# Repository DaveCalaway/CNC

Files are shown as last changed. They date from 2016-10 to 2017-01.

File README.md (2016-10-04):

##Improvement for Chinese 50W CO2 Laser Engraving Cutting Machine

This project was born for replace the original electronic chinese card, that moved the laser cutter machine, with **RAMPS 1.4** or **Arduino CNC Shield** .  
In addiction i made DIY driver for a much more laser power, take a look at "DIY_Driver_Controller" folder.  

Now the laser cutter machine can work with G-Code and Laser-Web app.

**The same principle is apply for all CNC/laser machines.**

**Status**: *beta*  

##Schematics
We have three types of schematics:
- Chinese original schematic
- RAMPS schematic
- CNC Shield schematic

##Meaning of the  laser's signals
The original schematic of RAMP at *original_diagram* reported two differents signals for the laser:
- **Laser Fire**, in my case, is the *Enable* switch for a laser, it's boolean.  
  In the *Chinese original schematic* is the green line, from electronic card "LO" to Laser Power Supply "TL". Active low for laser on.  
  You can also send this signal to the *Front Pannel*.  
  In the *RAMPS_schematic* it's "D5" pin.  
  In the *CNC Shield* it's GND if you used LO or 5V is you used TL.  

- **Laser PWM**, in my cose, is the PWM signal to drive the power's ramp.  
  In the *Chinese original schematic* is the white line, from *Frontal Pannel* to *Laser Power Supply* "IN".  

  In the *RAMPS_schematic* it's "D4" pin.  

  In the *CNC Shield*:
  * V3.0 it's "Z+"" pin end stop.
  * V3.1 it's "SpnDir" pin.  

##RAMPS 1.4 & CNC Shield built in

Remeber, CNC Shield works with GRBL and RAMPS works with Marlin. The only real different are the command: http://goo.gl/lHQ7T  

###Diode advise [ RAMPS ONLY ]
Ensure that the Power Supply 5v rail is connected to RAMPS I2C 5v pin and that the D1 diode is removed from the RAMPS board as shown in the wiring diagram. If this pin is not connected the laser will fire when you disconnect your ramps board from USB power.  

###Motors & Movement config
In my Laser cutter machine, *Chinese card*, i have 2 motors:  
1. **X-Motor**, Flexible flat ( Ribbon ) white cable with two Opto Endstops(X and Y).  
2. **Y-Motor**, 4 wires cable.  

In addiction i have one other motor, **Z-Motor**, for rise up and down the base.  

The motors are: **17hw4410n-03ad-z** and **17hw3448n-15ad**  
I written to *baolongmotor* and they gave me the datasheet. Take a look in my repository.  

###Voltage Ref
Reference [Page](http://goo.gl/8VKoRP)  
For *resistors*: R100 = 0.1 Ohm or R200 = 0.2 Ohm ecc....  
In my case, the *formula* goes:  `IRef = Vref/( 8 * 0.1)`  

For my motors i need about *Y-Vref* = 0,8 * 0,48A = 0,4V  and  *X-Vref* = 0,8 * 1A = 0,8V  

###Motor driver
It is important for a good movement take a note what types of [steppers drivers](http://goo.gl/u0PKhx) you will use:
- A4988 = Max. microsteps 16  
or  
- DRV8825 = Max. microsteps 32  

for decided how many *Jumpers* you could use: [RAMPS](http://goo.gl/bCJXzR) or [CNC](http://goo.gl/PzCEH5).  

Moreover take a look for a good orientation.

In my case, i buyed two A4988 and i will use only one jumper for 16 microsteps on RAMPS.  
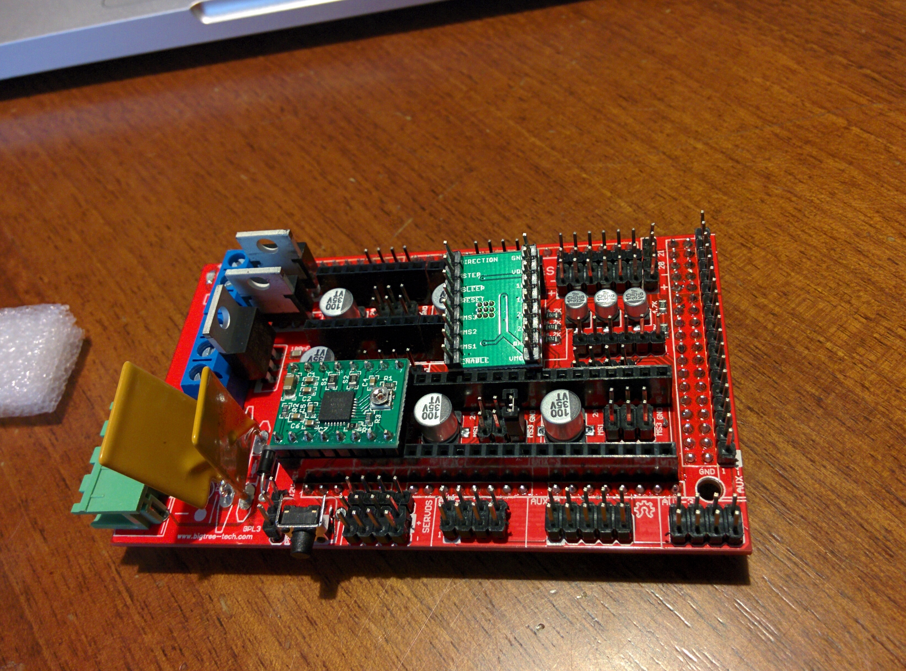
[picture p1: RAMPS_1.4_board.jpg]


If you want to use the single A4988, remember this schematic:  
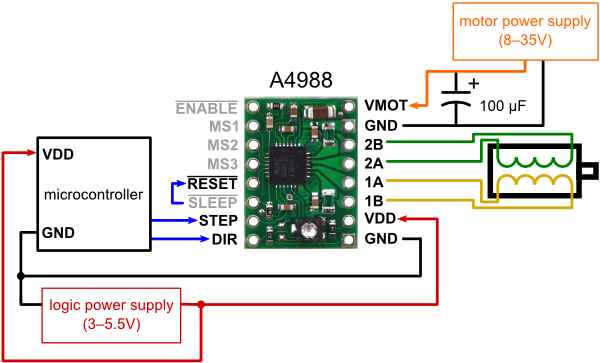
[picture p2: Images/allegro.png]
  

16 microsteps : MS1, MS2, and MS3 must be connected to HIGH ( 5V ).  

###Movement
We need to obtain the **Steps per millimeter**. *Reference page*: http://goo.gl/VHtbYw  
You could have two different type of driving systems:  
- belt driven systems  
- leadscrew driven systems  

In my case, i have the first drive system. Well, i need to know the **Belt pitch** (in mm) and **Pulley tooth number**.  

I used a red pen to count the pulley tooth, and the caliber for belt pitch.  

My results, *160.00*, save this number for the future:  

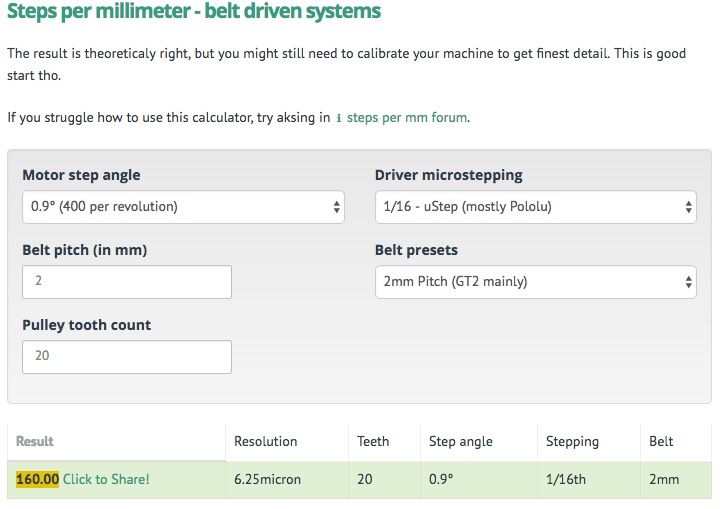
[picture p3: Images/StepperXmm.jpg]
  

###EndStop
My CNC machine has 2 Optical EndStop. They are wonderful for RAMPS 1.4.  

But if you are using CNC Shield, the Optical EndStop are unusable. You must use the meccanical endStop: http://goo.gl/bh0d5C  

##Configuring and compilation
###Ramps 1.4:
1. Install the arduino software IDE
2. Download the Marlin firmware to your PC and extract it
3. Start the Arduino IDE:
  1. Select Tools -> Board -> Arduino Mega 2560 or your microcontroller
  2. Select the correct serial port in Tools ->Serial Port
  3. Open Marlin.ino found in the 'Marlin' directory
  4. Click the Verify/Compile button
  5. Click the Upload button If all goes well the firmware is uploading and you'll see the led on your arduino flashing wildly. The Arduino IDE will tell you when it has finished uploading.

###CNC shield GRBL v0.9 or greaters (PWM Spindle + Soft limits)
 1. Install the arduino software IDE
 2. Load in Arduino IDE the GRBL : https://goo.gl/1aiAtr
 3. Removed Z axi : https://goo.gl/0uzKYu
 4. Load edited Gcode.

##LaserWeb2 and UniversalGcodeSender
**[LaserWeb](https://goo.gl/PNTPV3)** it's an Host software for Lasercutters/Engravers , it takes many types of files and convert them in Gcode.  
NB. take a look at the version you would like to install, each version has different features.  

**UniversalGcodeSender** it takes the Gcode, made by LaserWeb, and send them to Arduino. It's in repository. Set the baud rate to 115200.  

This program are used to set all base commands on Gcode or Marlin.

For any Gcode interpreter **$$** show the principle machine setting - **$** used to set a command .  

[Marlin](https://goo.gl/VVwOUN) code for RAMPS:  
* Steps per millimeter
  * M92 X160.00 (x, step/mm)
  * M92 Y160.00 (x, step/mm)
* Hard-limits / Soft-limits
  * ....

[GRBL](https://goo.gl/kcWGXD) code for CNC:
* Steps per millimeter
  * $100=314.961 (x, step/mm)
  * $101=314.961 (y, step/mm)
* Hard-limits / Soft-limits / Homing cycle
  * $21 = 1
  * $20 = 1
  * $22 = 1
* Test Homing: (if you need to invert direction use $23)
  * $H
* Test the laser with this commands, it's driven by PWM signal in a ranch of 0-1000
  * M5 => laser off
  * S100 => set laser power to 10% but not fire
  * S10 + M3 => set laser power to 1% and fire

##Implementation  

###Physical endstop  
This machine has only 2 Opto-endstop ( X+ and Y+ ), but for more security i made two supports for two additional physical endspot ( X- and Y-) .  

I got two physical endstop on my CD/DVD reader/writer.  
Using my 3D printer i made a nice supports, take a look at *physical_endstop's* folder.  

**Setting for work in the 2nd quadrant**  

  

**GRBL**  
* $H // go at endstops
* G10 L2 P2 X-550Y-380 // set work position (it's different from the machine position) at X550 & Y380 coordinates
* G55 // force the machine for working at work position coordinates
now if you do *G0 X0Y0* the machine will go at origin (0,0) axis ( lower left corner, Cartesian remember ).

After these settings, remember to put *$H* and *G55* at starter code.  

###Endstop Filters  

I added pull-up and RC filters on X-Y Endstops for avoid false limits trigger.  

###Top coverage switch  
In my machine i have 3 types of security systems:  
1. Enable/Disable laser in front of machine  
2. Panic button, disable all machine power  
3. Water level check  
The numbers 1 & 3 must be lower to enable the laser power. They are in series on the same line, from to *WP* pin on power supply.  

For many reasone i would like to add another security system, on Top coverage.  

The system it's pretty easy, i added a meccanical switch in the same line of 1 & 3 devices.  

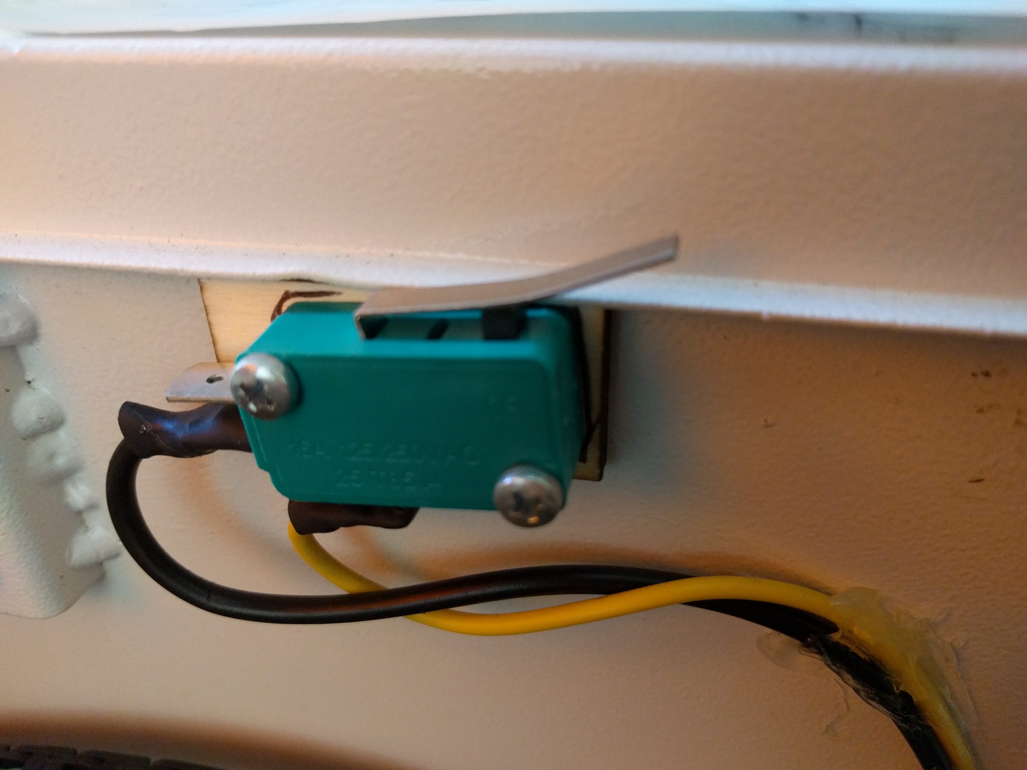
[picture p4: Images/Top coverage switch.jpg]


##Future implementations
[x] Top coverage switch  
[x] Physical endstop  
[x] Endstop Filters  
[x] DIY driver Control: new schematic, with Optocoupler, for reduce false "Hard-limits"  
[ ] Z axis  
[ ] Thermal shutdown  
soon....

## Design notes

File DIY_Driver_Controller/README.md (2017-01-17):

##DIY CNC Driver Controller

This project was born for replace the **Arduino CNC Shield**, it presents noise on EndStops and Motors.  

####Details:
- Optocoupler for better isolation for Arduino's signals to drivers
- New RC filters for EndStops   

**Status**: *beta*  

Thank you, Valentino Vaia, for all your assistance and breadboard PCB.

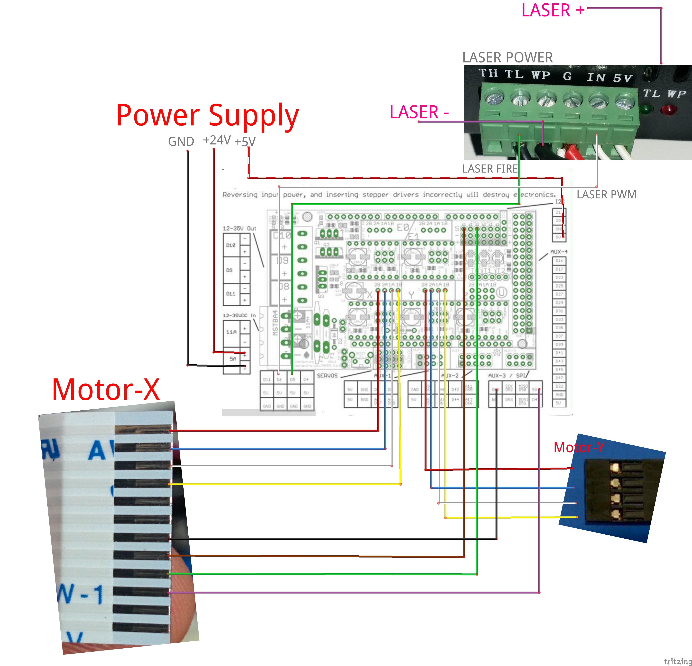
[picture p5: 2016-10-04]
RAMPS_schematic_V0.1.jpg

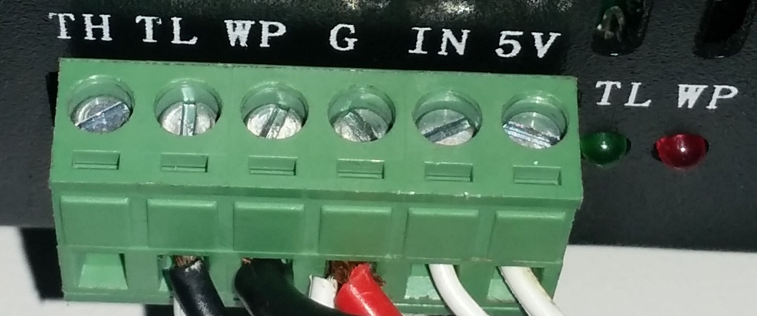
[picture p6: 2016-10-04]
Images/laser_power.jpg

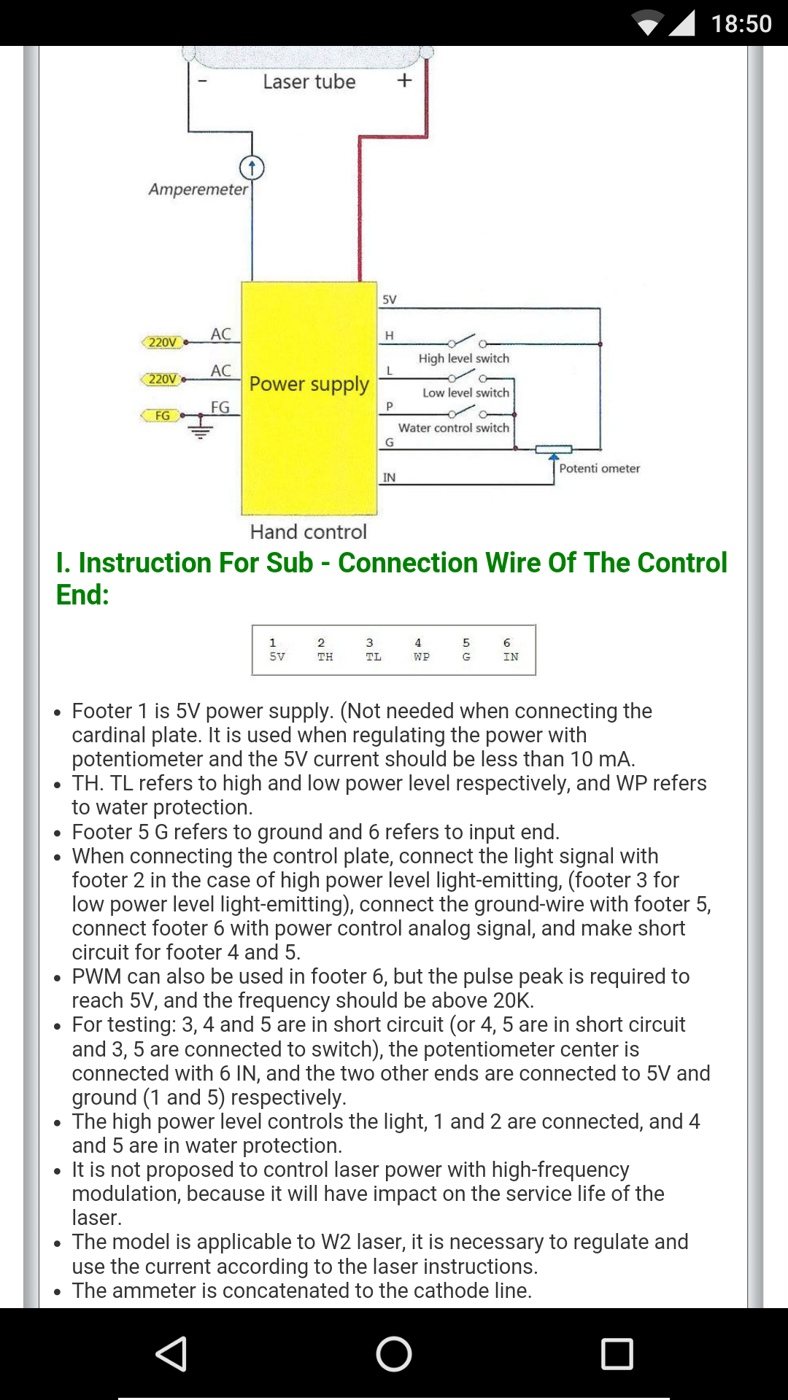
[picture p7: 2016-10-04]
Power_supply.png

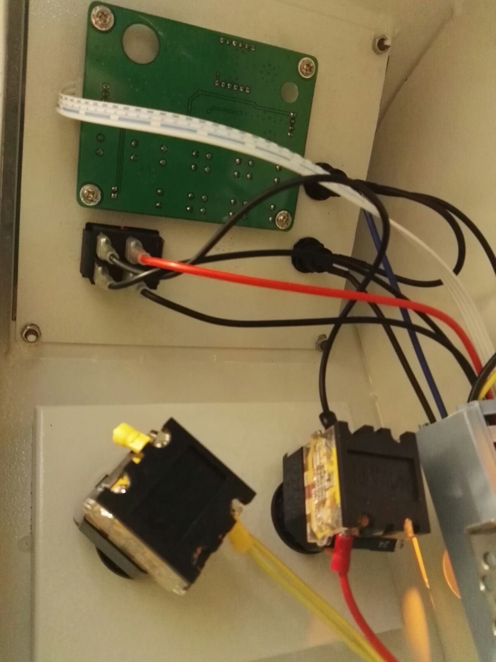
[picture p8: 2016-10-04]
Images/Frontal back2.jpg

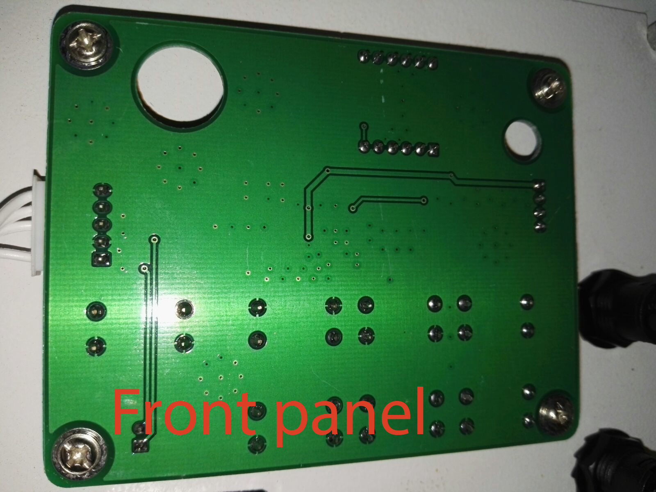
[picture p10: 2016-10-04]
Images/Frontal back_1.png

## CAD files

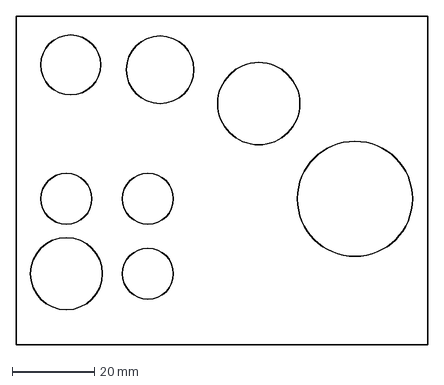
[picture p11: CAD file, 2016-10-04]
Examples/test cnc.dxf
100.0 x 80.0 mm

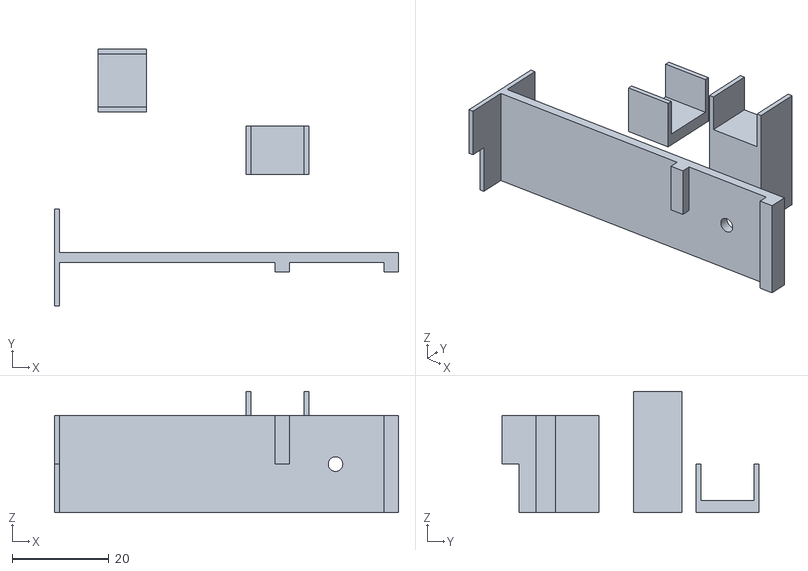
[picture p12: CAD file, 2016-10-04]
physical_endstop/Support_-x-y.stl
71.0 x 53.0 x 25.0

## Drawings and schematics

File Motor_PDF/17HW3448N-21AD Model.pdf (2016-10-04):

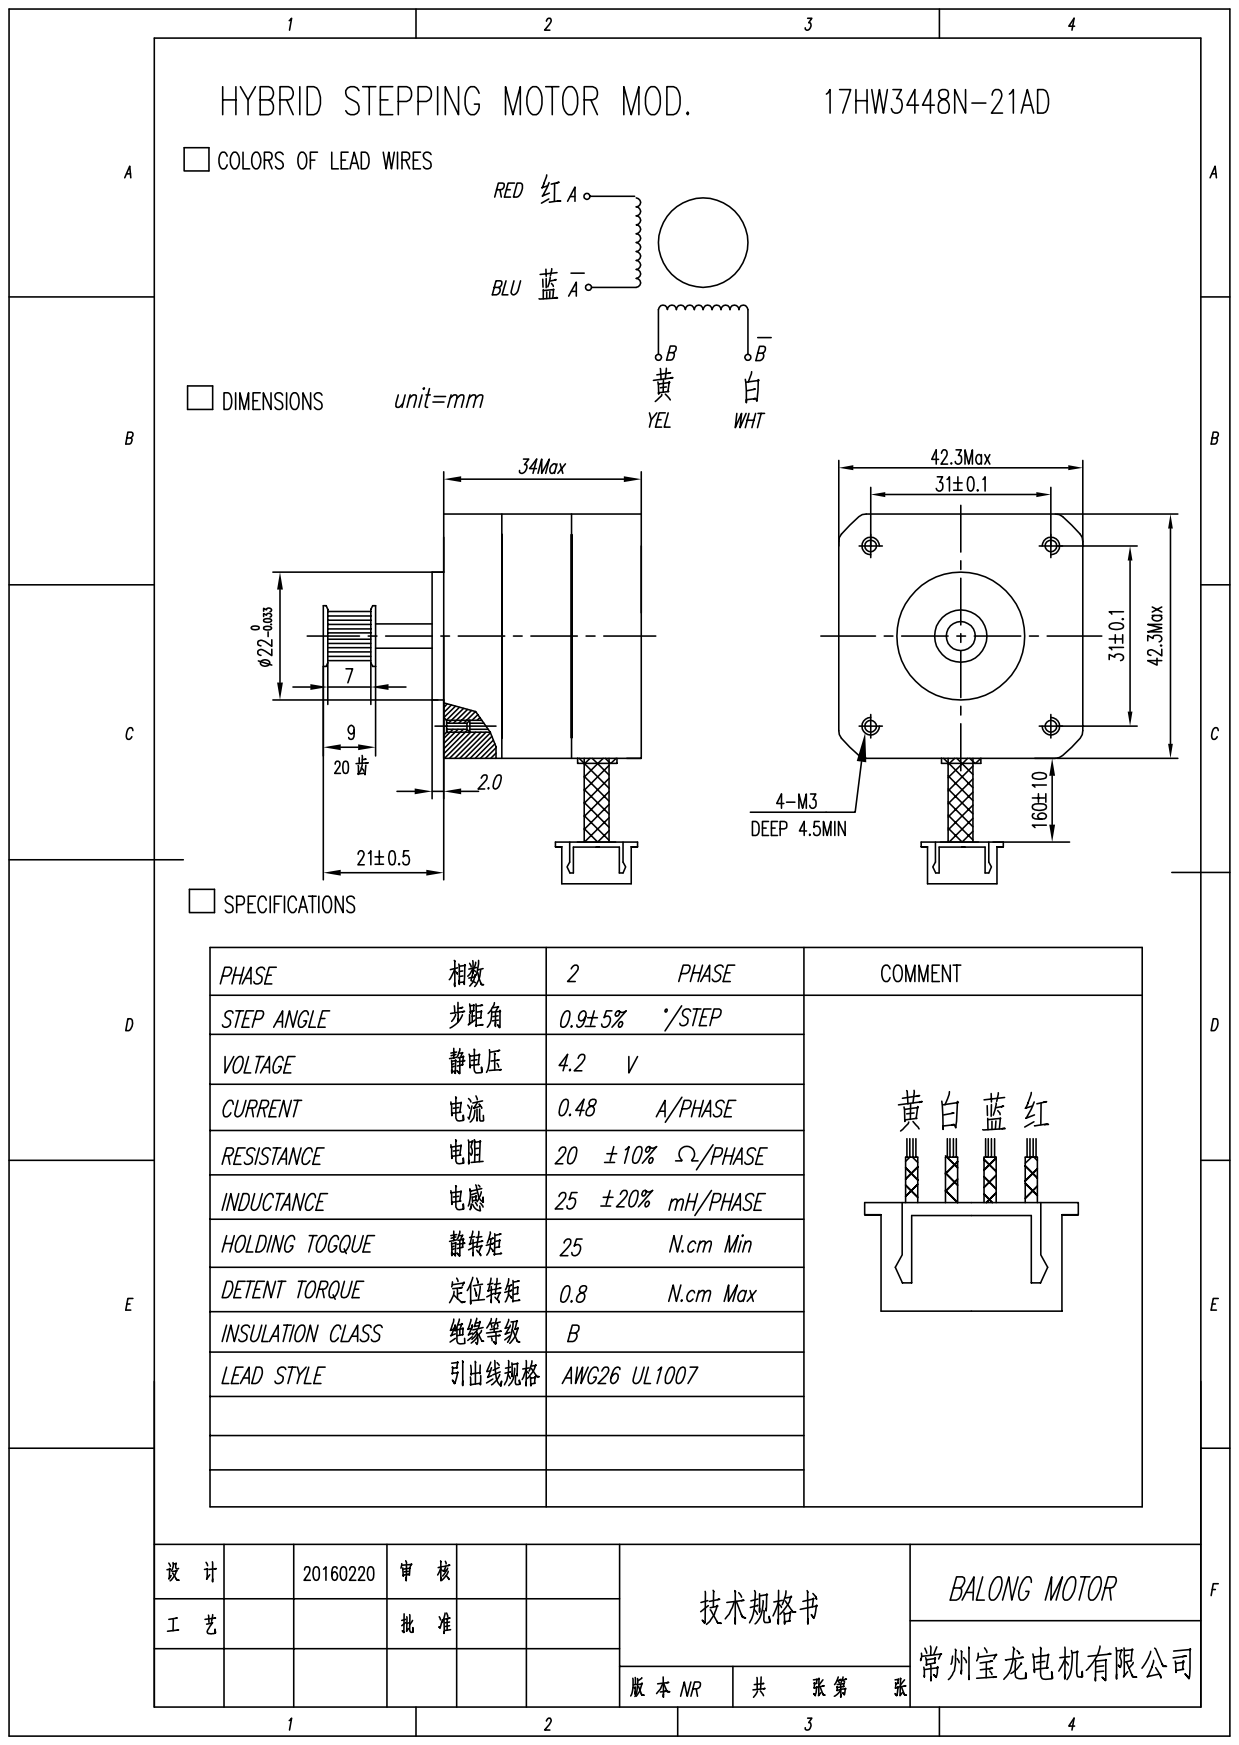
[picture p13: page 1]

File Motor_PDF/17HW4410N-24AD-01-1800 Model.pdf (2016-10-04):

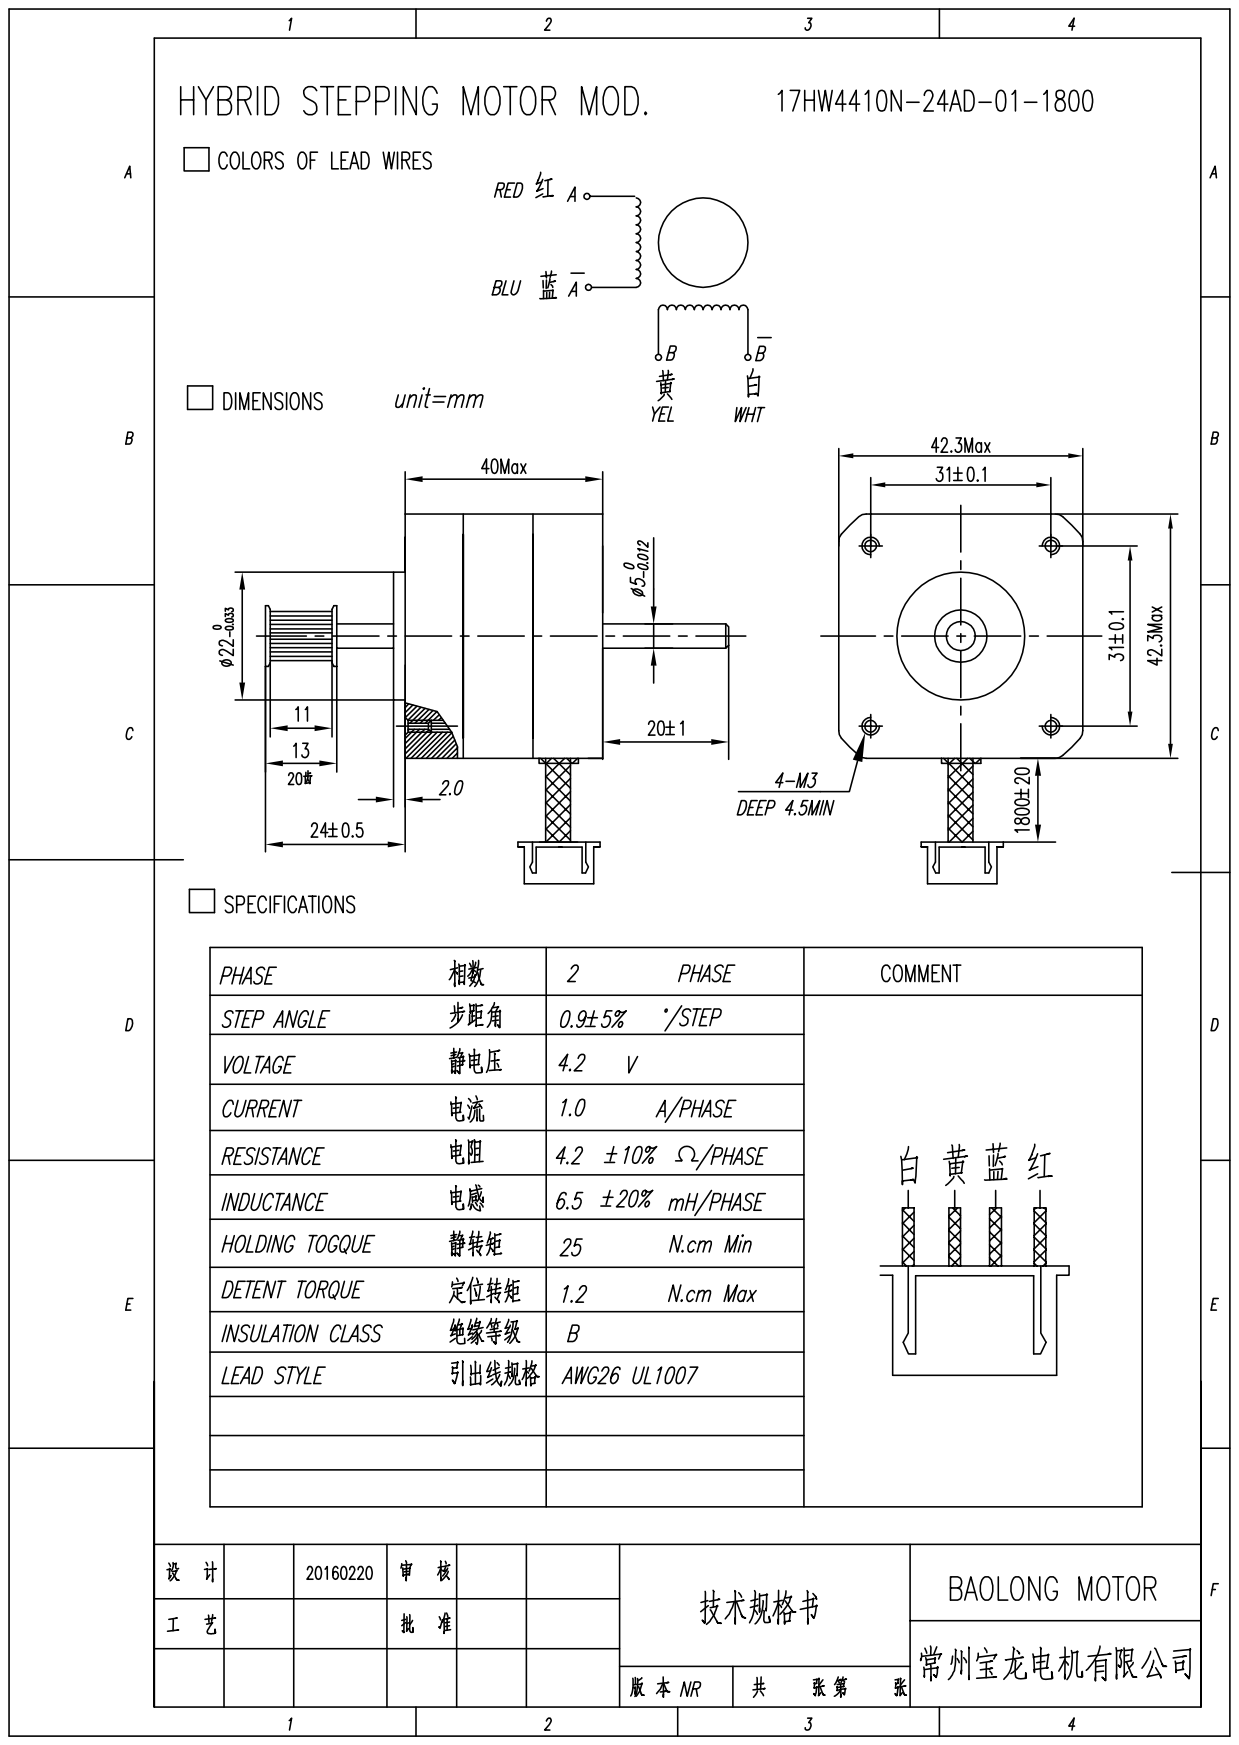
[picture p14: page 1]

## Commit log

2016-12-03 V0.3
    Fixed filters. Thx Federico Altiero & Valentino Vaia.
    [Driver.fzz]
2017-01-17 breadboard PCB
2017-02-07 beta 0.4 fixed inverted pins
    [Driver.fzz]
2017-02-13 Added enable's optocoupler and 7805
    [Driver.fzz]
2017-02-15 fixed command gnd optocop
    [Driver.fzz]
